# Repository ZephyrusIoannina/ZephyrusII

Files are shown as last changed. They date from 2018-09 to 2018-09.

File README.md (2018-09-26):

## Zephyrus II

This package was created by the Zephyrus II CanSat team (Ioannina - Greece) for the CanSats in Europe 2018 Launch campaign.
Feel free to use it as you please for future missions.
A reference to our team is most welcome but not obligatory.

The package contains:
1. Our source code for our flight module our payload and our groundstation with libraries. Extra effort was taken in translating our rem inside the code since it was mostly Greek
2. Our solidworks models
3. A calculations spreadsheet for data collected by our cansat
4. A spreadsheet with our calculation model for our descent
5. A list of commands for our cansat.
6. Electrical diagramms for both our modules

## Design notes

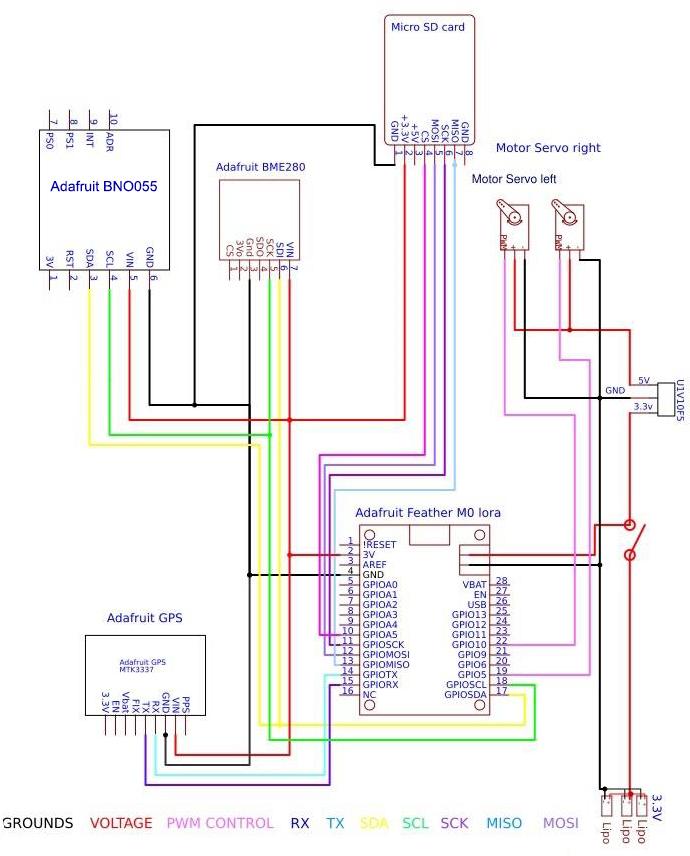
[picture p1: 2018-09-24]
flight electronics.jpg

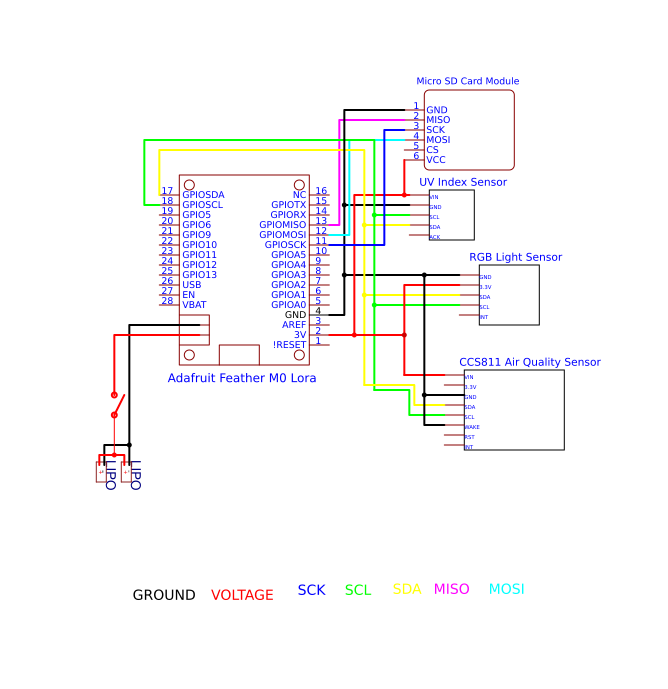
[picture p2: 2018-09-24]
payload.png

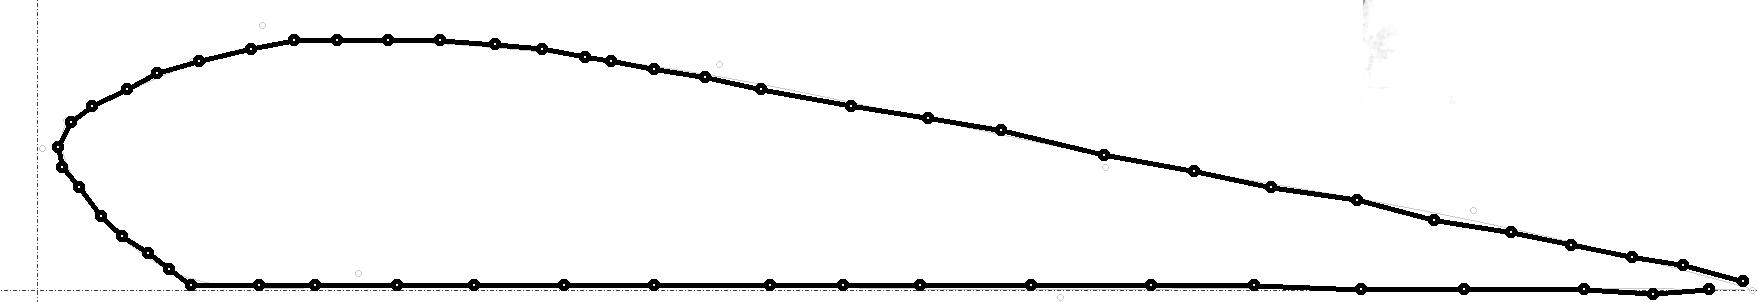
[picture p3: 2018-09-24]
zephyrusIIsolidworks/parachute/NS_foil.jpg

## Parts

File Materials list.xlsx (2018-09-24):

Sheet: Γενικά Υλικά για παραγγελίες
Αλεξίπτωτο |  |  |  |  | Ποσότητα | Τιμή μοναδας | Τελικό ποσό | Απαιτούνται
 | Ύφασμα | http://www.metropolis-drachen.de/en/Kite-materials/Cloth-Fabric/Spinnaker-fabrics/Spinnaker-Skytex-27.html |  |  | 8 | 11.90 € | 95.20 € | 1 | 11.90 €
 | Αυτοκόλητα επιδιόρθωσης | http://www.metropolis-drachen.de/en/Kite-materials/Stripes-Tapes/Tapes/Spi-repair-tape.html |  |  | 2 | 1.95 € | 3.90 € | 0 | 0.00 €
Flight Module
 | Radio - Arduino | https://gr.mouser.com/Search/ProductDetail.aspx?R=3179virtualkey54850000virtualkey485-3179 | 2km χαλαρα με απλη κεραια λεει | επι 4 μάλλον | 4 | 29.71 € | 118.84 € | 2 | 59.42 €
 | GPS | https://gr.mouser.com/Search/ProductDetail.aspx?R=746virtualkey54850000virtualkey485-746 | Serial |  | 2 | 33.96 € | 67.92 € | 1 | 33.96 €
 | Μαγνητόμετρο-Accel - Gyro | https://gr.mouser.com/ProductDetail/Adafruit/2472?qs=sGAEpiMZZMsMyYRRhGMFNuFoI0IaQxst8qeHhFTzrMI%3d | I2C |  | 2 | 30.00 € | 60.00 € | 1 | 30.00 €
 | Πίεση Θερμοκρασία Υγρασία | https://gr.mouser.com/Search/ProductDetail.aspx?R=2652virtualkey54850000virtualkey485-2652 | I2C |  | 2 | 16.96 € | 33.92 € | 1 | 16.96 €
ΙΔΙΟ μαγαζί | Esc | https://www.premium-modellbau.de/emax-bullet-20a-fpv-race-brushless-esc-2s-4s-3-5g-dshot-blheli-s |  |  | 2 | 15.90 € | 31.80 € | 1 | 15.90 €
 | Κινητήρας | https://www.premium-modellbau.de/emax-rs1106-fpv-racing-brushless-motor-7500kv-2s-7g | ΠΡΟΣΟΧΗ το 7500KV επιλέγουμε |  | 2 | 12.99 € | 25.98 € | 1 | 12.99 €
 | Έλικα (2x10) | https://www.premium-modellbau.de/t2345-emax-10x-paar-race-propeller-f.-rs1104-babyhawk-in-transparent |  | 20 κομμάτια | 1 | 19.95 € | 19.90 € | 0.05 | 1.00 €
 | Μπαταρία κινητήρα | http://www.giatrakos.gr/product/9793/perifereiaka-mpataries,-fortistes-mpataries-lipo-life-lrp-7.4v-900mah-vtec- |  |  | 2 | 15.00 € | 30.00 € | 1 | 15.00 €
 | SERVO PWM 120μοίρες | https://grobotronics.com/servo-micro-1.8kg.cm-metal-gears-feetech-fs90mg.html |  |  | 4 | 7.90 € | 31.60 € | 2 | 15.80 €
optional | Proximity Sensor | https://grobotronics.com/vcnl4000-proximity-light-sensor.html | I2C |  | 0 | 9.20 € | 0.00 € | 0 | 0.00 €
 | SD breakout | https://gr.mouser.com/Search/ProductDetail.aspx?R=254virtualkey54850000virtualkey485-254 |  |  | 4 | 6.38 € | 25.52 € | 2 | 12.76 €
 | μπαταρια διπλή flight | https://www.ebay.com/itm/3-7V-700mAh-Lipo-polymer-Li-Battery-cells-for-MP3-GPS-Camera-mobile-phone-702050/172452417339 |  |  | 4 | 6.40 € | 25.60 € | 2 | 12.80 € | http://www.giatrakos.gr/product/9623/perifereiaka-mpataries,-fortistes-mpataries-lipo-life-3.7v-750mah-syma-battery-
Payload Module ϊσως βολεύει 3,3 Volt όλο το module
 | Radio - Arduino | https://www.adafruit.com/product/3179
 | μπαταρία payload | https://www.ebay.com/itm/2pcs-3-7V-700mAh-lipo-Polymer-li-cells-Battery-For-Mp3-GPS-camera-DVD-PAD-803030/262501223843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 | διπλή |  | 4 | 8.93 € | 35.72 € | 2 | 17.86 €
 | UV sensor | https://gr.mouser.com/Search/ProductDetail.aspx?R=2899virtualkey54850000virtualkey485-2899 | I2C |  | 2 | 5.06 € | 10.12 € | 1 | 5.06 €
 | Light sensor | https://gr.mouser.com/Search/ProductDetail.aspx?R=SEN-12829virtualkey54740000virtualkey474-SEN-12829 | I2C | RGB!! | 2 | 6.76 € | 13.52 € | 1 | 6.76 €
out of stock (μόνο1) | CO2 VOC | https://www.hellasdigital.gr/electronics/sensors/gas-sensors/adafruit-ccs811-air-quality-sensor-breakout-voc-and-eco2/ |  |  | 2 | 24.80 € | 49.60 € | 1 | 24.80 € |  | out of stock
 |  |  |  | Σύνολο |  |  | 679.14 € |  | 292.97 €
 |  |  |  |  |  |  |  |  | Κόστος Cansat
 | Σταθεροποιητής | Voltage Regulator L7805CV - 5V 1.5AΚωδικός: 05-00078050 (https://grobotronics.com/voltage-regulator-l7805cv-5v-1.5a.html)
 | Σταθεροποιητής | Voltage Regulator LD1117 - 3.3V 800mAΚωδικός: 05-01117330 (https://grobotronics.com/voltage-regulator-ld1117-3.3v-800ma.html)

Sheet: Κοστολόγιο Υλικών Cansat
Αλεξίπτωτο |  |  |  |  | Ποσότητα | Τιμή μοναδας | Τελικό ποσό
 | Ύφασμα | http://www.metropolis-drachen.de/en/Kite-materials/Cloth-Fabric/Spinnaker-fabrics/Spinnaker-Skytex-27.html |  |  | 1 | 11.90 € | 11.90 €
 | Αυτοκόλητα επιδιόρθωσης | http://www.metropolis-drachen.de/en/Kite-materials/Stripes-Tapes/Tapes/Spi-repair-tape.html |  |  | 1 | 1.95 € | 1.95 €
 | Σχοινιά
Flight Module
 | Radio - Arduino | https://gr.mouser.com/Search/ProductDetail.aspx?R=3179virtualkey54850000virtualkey485-3179 | 2km χαλαρα με απλη κεραια λεει | επι 4 μάλλον | 1 | 29.71 € | 29.71 €
 | GPS | https://gr.mouser.com/Search/ProductDetail.aspx?R=746virtualkey54850000virtualkey485-746 | Serial |  | 1 | 33.96 € | 33.96 €
 | Μαγνητόμετρο-Accel - Gyro | https://gr.mouser.com/ProductDetail/Adafruit/2472?qs=sGAEpiMZZMsMyYRRhGMFNuFoI0IaQxst8qeHhFTzrMI%3d | I2C |  | 1 | 30.00 € | 30.00 €
 | Πίεση Θερμοκρασία Υγρασία | https://gr.mouser.com/Search/ProductDetail.aspx?R=2652virtualkey54850000virtualkey485-2652 | I2C |  | 1 | 16.96 € | 16.96 €
ΙΔΙΟ μαγαζί | Esc | https://www.premium-modellbau.de/emax-bullet-20a-fpv-race-brushless-esc-2s-4s-3-5g-dshot-blheli-s |  |  | 0 |  | 0.00 €
 | Κινητήρας | https://www.premium-modellbau.de/emax-rs1106-fpv-racing-brushless-motor-7500kv-2s-7g | ΠΡΟΣΟΧΗ το 7500KV επιλέγουμε |  |  |  | 0.00 €
 | Έλικα (2x10) | https://www.premium-modellbau.de/t2345-emax-10x-paar-race-propeller-f.-rs1104-babyhawk-in-transparent |  |  |  |  | 1.00 €
 | Μπαταρία | http://www.giatrakos.gr/product/9793/perifereiaka-mpataries,-fortistes-mpataries-lipo-life-lrp-7.4v-900mah-vtec- |  |  | 1 | 15.00 € | 15.00 € | απο giatrakos
 | SERVO PWM 120μοίρες | https://grobotronics.com/servo-micro-1.8kg.cm-metal-gears-feetech-fs90mg.html |  |  | 2 | 7.90 € | 15.80 € | απο grobotr
 | SD breakout | https://gr.mouser.com/Search/ProductDetail.aspx?R=254virtualkey54850000virtualkey485-254 |  |  | 1 | 6.38 € | 6.38 €
 | μπαταρια 2 | http://www.giatrakos.gr/product/9623/perifereiaka-mpataries,-fortistes-mpataries-lipo-life-3.7v-750mah-syma-battery- |  |  | 2 | 10.00 € | 20.00 € | απο giatrakos
Payload Module ϊσως βολεύει 3,3 Volt όλο το module
 | Radio - Arduino | https://gr.mouser.com/Search/ProductDetail.aspx?R=3179virtualkey54850000virtualkey485-3179 |  |  | 1 | 29.71 € | 29.71 € | https://www.adafruit.com/product/3179
 | UV sensor | https://gr.mouser.com/Search/ProductDetail.aspx?R=2899virtualkey54850000virtualkey485-2899 | I2C |  | 1 | 5.06 € | 5.06 €
 | Light sensor | https://gr.mouser.com/Search/ProductDetail.aspx?R=SEN-12829virtualkey54740000virtualkey474-SEN-12829 | I2C | RGB!! | 1 | 6.76 € | 6.76 €
 | CO2 VOC | https://www.hellasdigital.gr/electronics/sensors/gas-sensors/adafruit-ccs811-air-quality-sensor-breakout-voc-and-eco2/ |  |  | 1 | 24.80 € | 24.80 € | https://gr.mouser.com/Search/ProductDetail.aspx?R=3566virtualkey54850000virtualkey485-3566 | out of stock
 |  |  |  | Σύνολο |  |  | 248.99 €

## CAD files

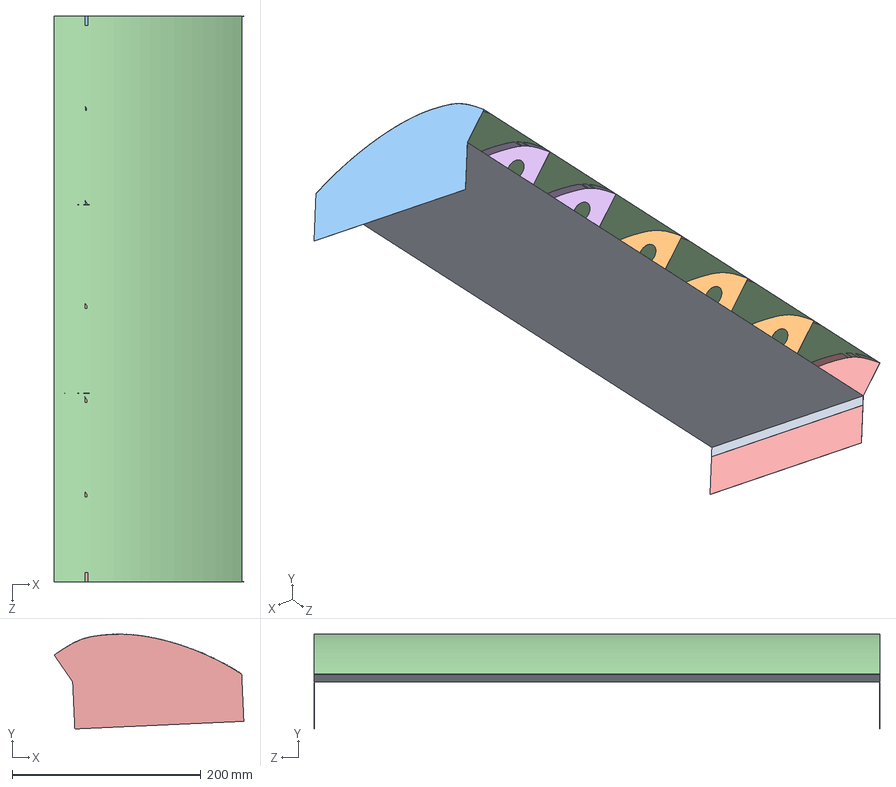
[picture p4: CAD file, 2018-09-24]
zephyrusIIsolidworks/parachute/Assem1a.SLDASM
201.2 x 100.7 x 600.2 mm
bottom
compartement x 3
sideb
top
side
compartement_L x 2

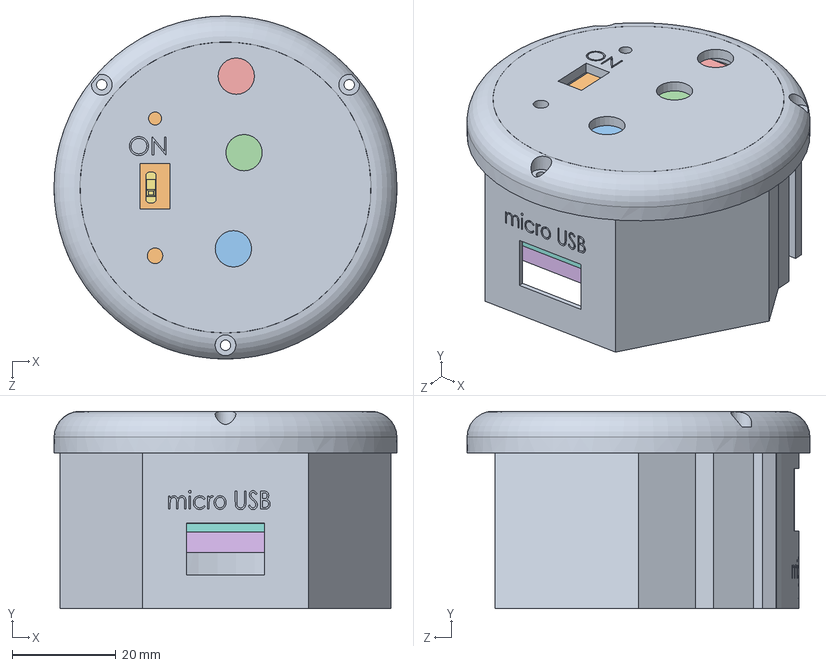
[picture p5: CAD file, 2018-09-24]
zephyrusIIsolidworks/PAYLOAD_ASSEMB.SLDASM
66.0 x 38.0 x 66.0 mm
payload
perfboard_pl
CCS811
ISL29125
VEML6070
featherM0LORA
SMD Switch
perfboard_pl_2
perfboard_pl_3
Micro SD
Lipo750A

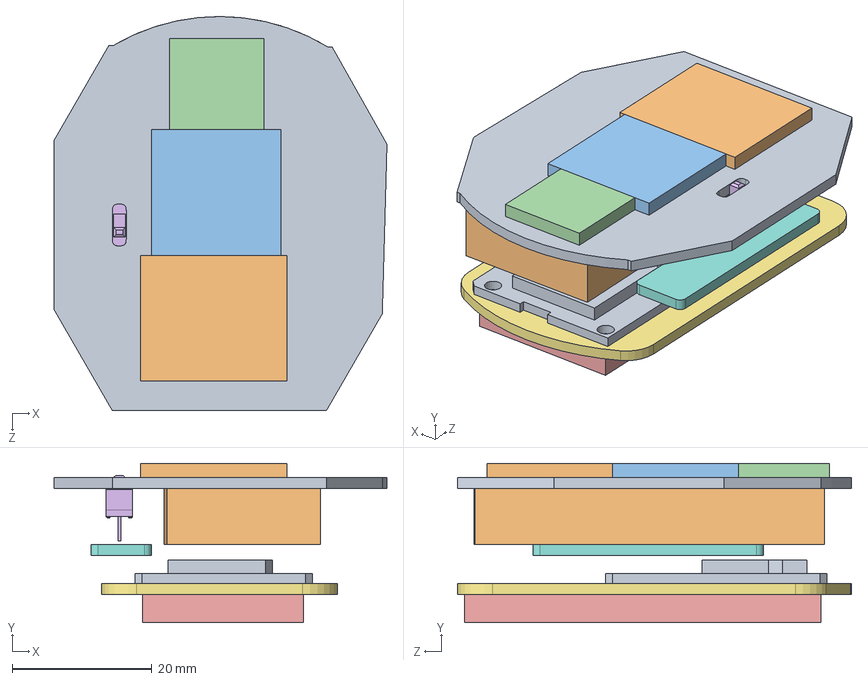
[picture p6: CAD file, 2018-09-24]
zephyrusIIsolidworks/perf_payload.SLDASM
47.7 x 22.8 x 56.4 mm
perfboard_pl
CCS811
ISL29125
VEML6070
featherM0LORA
SMD Switch
perfboard_pl_2
perfboard_pl_3
Micro SD
Lipo750A

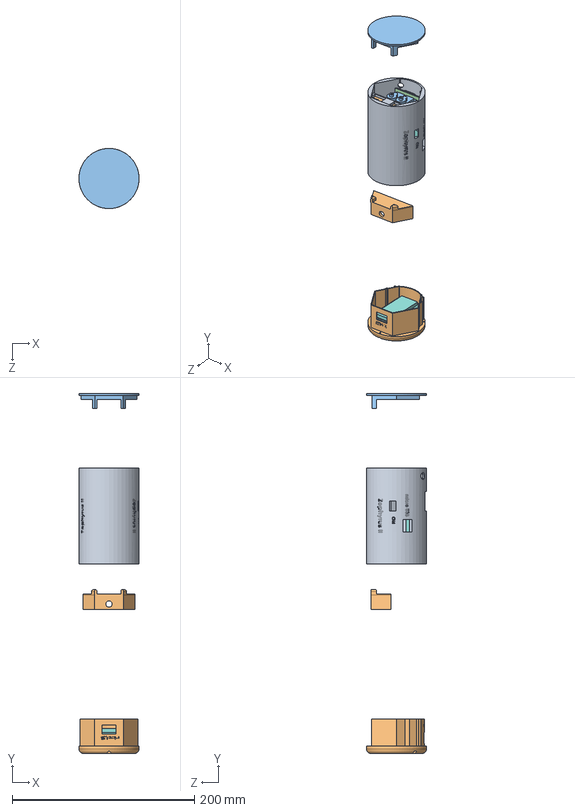
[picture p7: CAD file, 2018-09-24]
zephyrusIIsolidworks/Assem1nobat2.SLDASM
66.0 x 395.0 x 66.0 mm
Flight_down_nobat_2
Lipo750A x 4
Tower Pro 9g Micro Servo SG90 x 2
perfboard
Adafruit BME280
GPS
BNO055
featherM0LORA x 2
Micro SD x 2
payload
perfboard_pl
CCS811
ISL29125
VEML6070
SMD Switch
perfboard_pl_2
perfboard_pl_3
batterycap
backcap

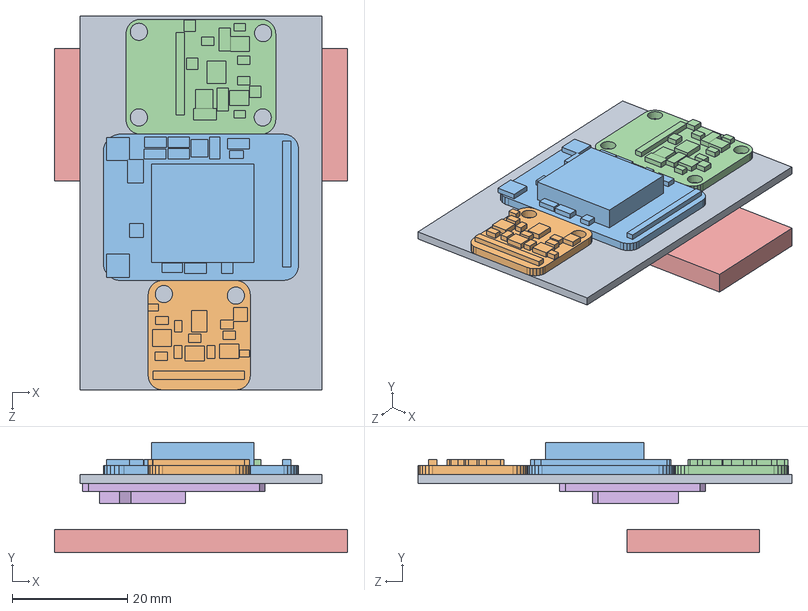
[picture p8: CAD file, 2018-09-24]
zephyrusIIsolidworks/perf_flight.SLDASM
51.0 x 19.2 x 65.0 mm
perfboard
Adafruit BME280
GPS
BNO055
featherM0LORA
Micro SD

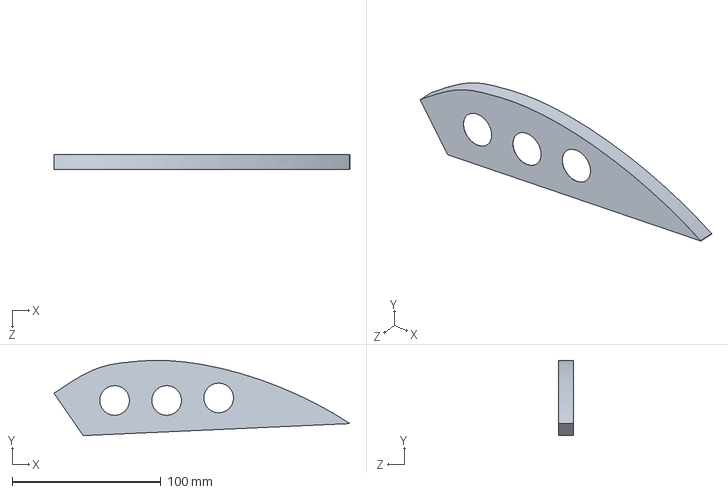
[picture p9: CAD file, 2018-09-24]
zephyrusIIsolidworks/parachute/compartement_L.SLDPRT
199.0 x 50.6 x 10.1 mm

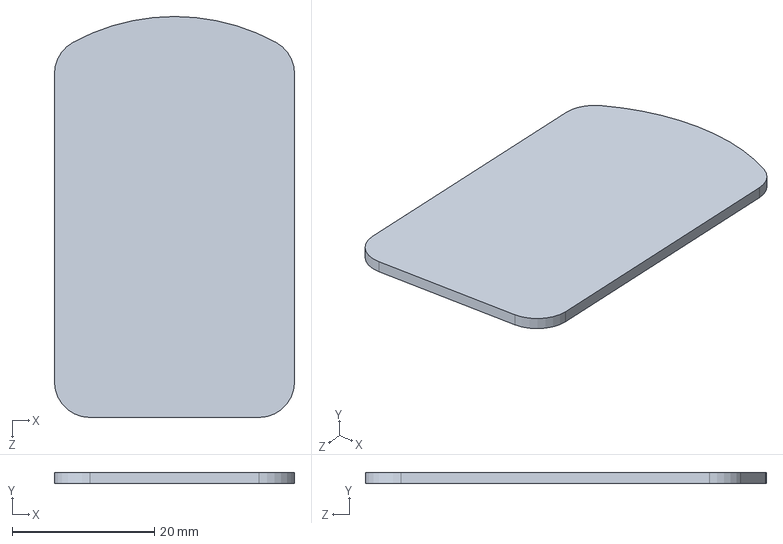
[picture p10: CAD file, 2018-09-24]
zephyrusIIsolidworks/perfboard_pl_2.SLDPRT
33.8 x 1.60 x 56.4 mm

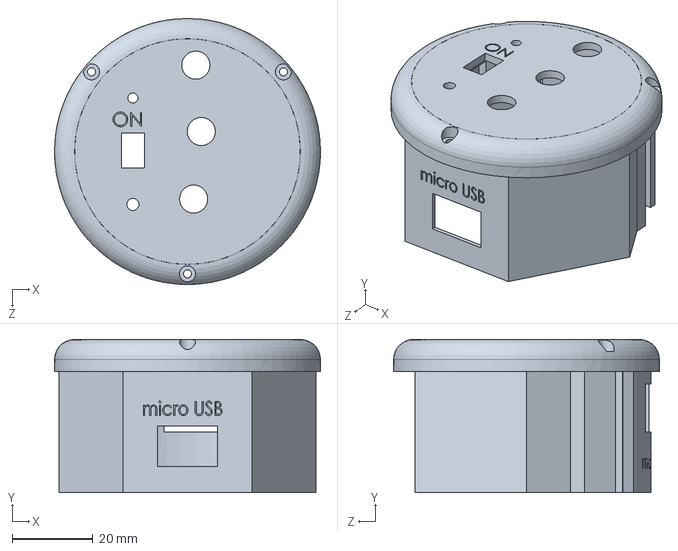
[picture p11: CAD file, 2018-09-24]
zephyrusIIsolidworks/payload.SLDPRT
66.0 x 38.0 x 66.0 mm

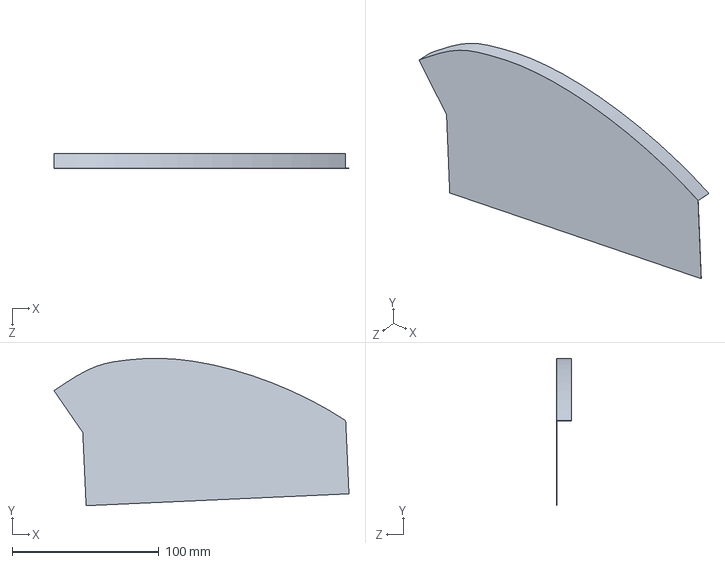
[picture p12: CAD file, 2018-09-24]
zephyrusIIsolidworks/parachute/side.SLDPRT
201.2 x 100.5 x 10.0 mm

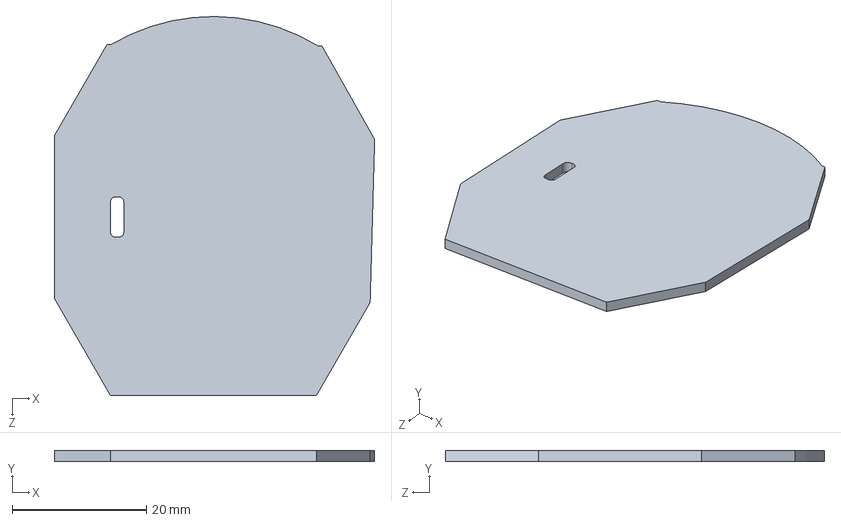
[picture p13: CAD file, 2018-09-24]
zephyrusIIsolidworks/perfboard_pl.SLDPRT
47.7 x 1.60 x 56.4 mm

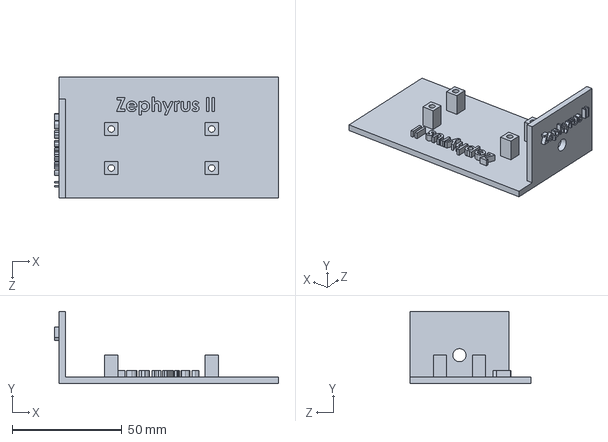
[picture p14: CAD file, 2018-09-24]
zephyrusIIsolidworks/groundstation.SLDPRT
102.0 x 33.0 x 55.0 mm

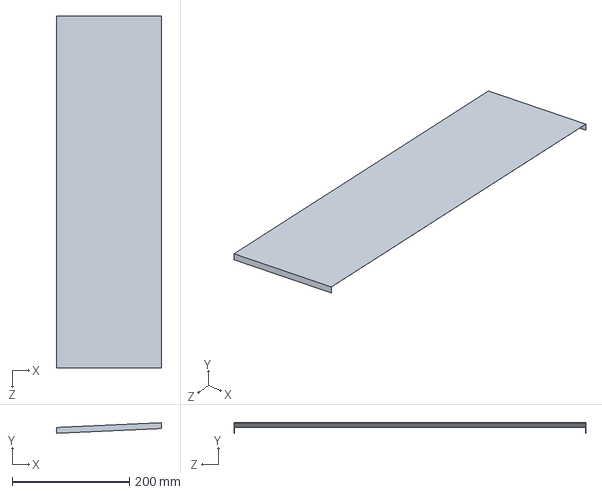
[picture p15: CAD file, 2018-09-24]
zephyrusIIsolidworks/parachute/bottom.SLDPRT
179.8 x 18.1 x 600.0 mm

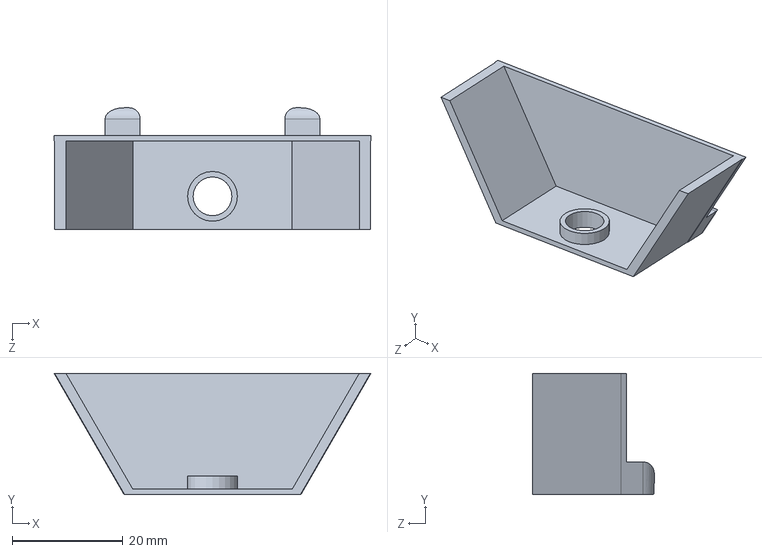
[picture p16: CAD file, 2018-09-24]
zephyrusIIsolidworks/batterycap.SLDPRT
57.2 x 21.9 x 22.0 mm

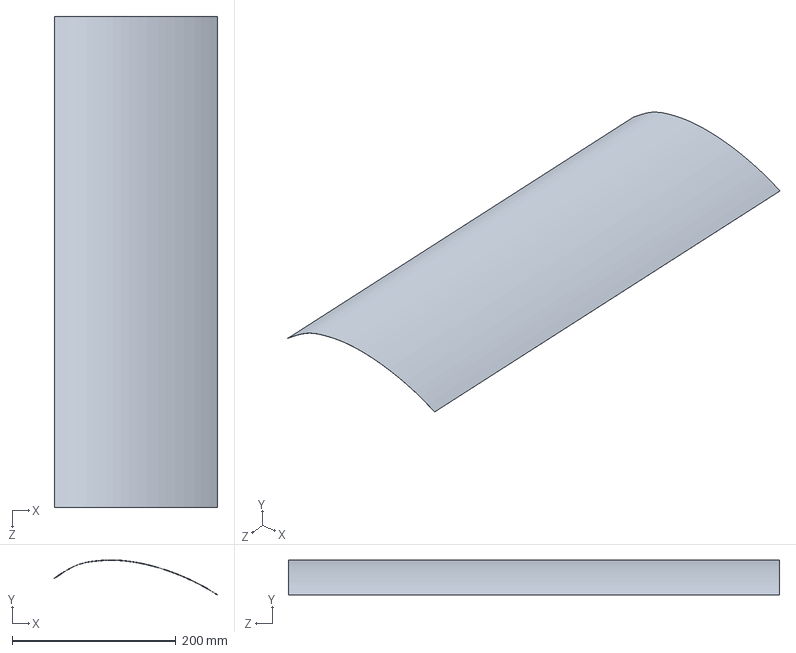
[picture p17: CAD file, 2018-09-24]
zephyrusIIsolidworks/parachute/top.SLDPRT
199.1 x 42.6 x 600.2 mm

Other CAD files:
zephyrusIIsolidworks/parachute/compartement.SLDPRT
zephyrusIIsolidworks/parachute/sideb.SLDPRT
zephyrusIIsolidworks/perfboard_pl_3.SLDPRT
zephyrusIIsolidworks/parachute/compartement_L_2.SLDPRT
zephyrusIIsolidworks/Flight_down_nobat_2.SLDPRT
zephyrusIIsolidworks/backcap.SLDPRT
zephyrusIIsolidworks/parachute/compartement_sketch.SLDDRW
zephyrusIIsolidworks/parachute/compartement_sketch.SLDPRT
zephyrusIIsolidworks/parachute/compartement_sketch_large.STL
zephyrusIIsolidworks/perfboard.SLDPRT

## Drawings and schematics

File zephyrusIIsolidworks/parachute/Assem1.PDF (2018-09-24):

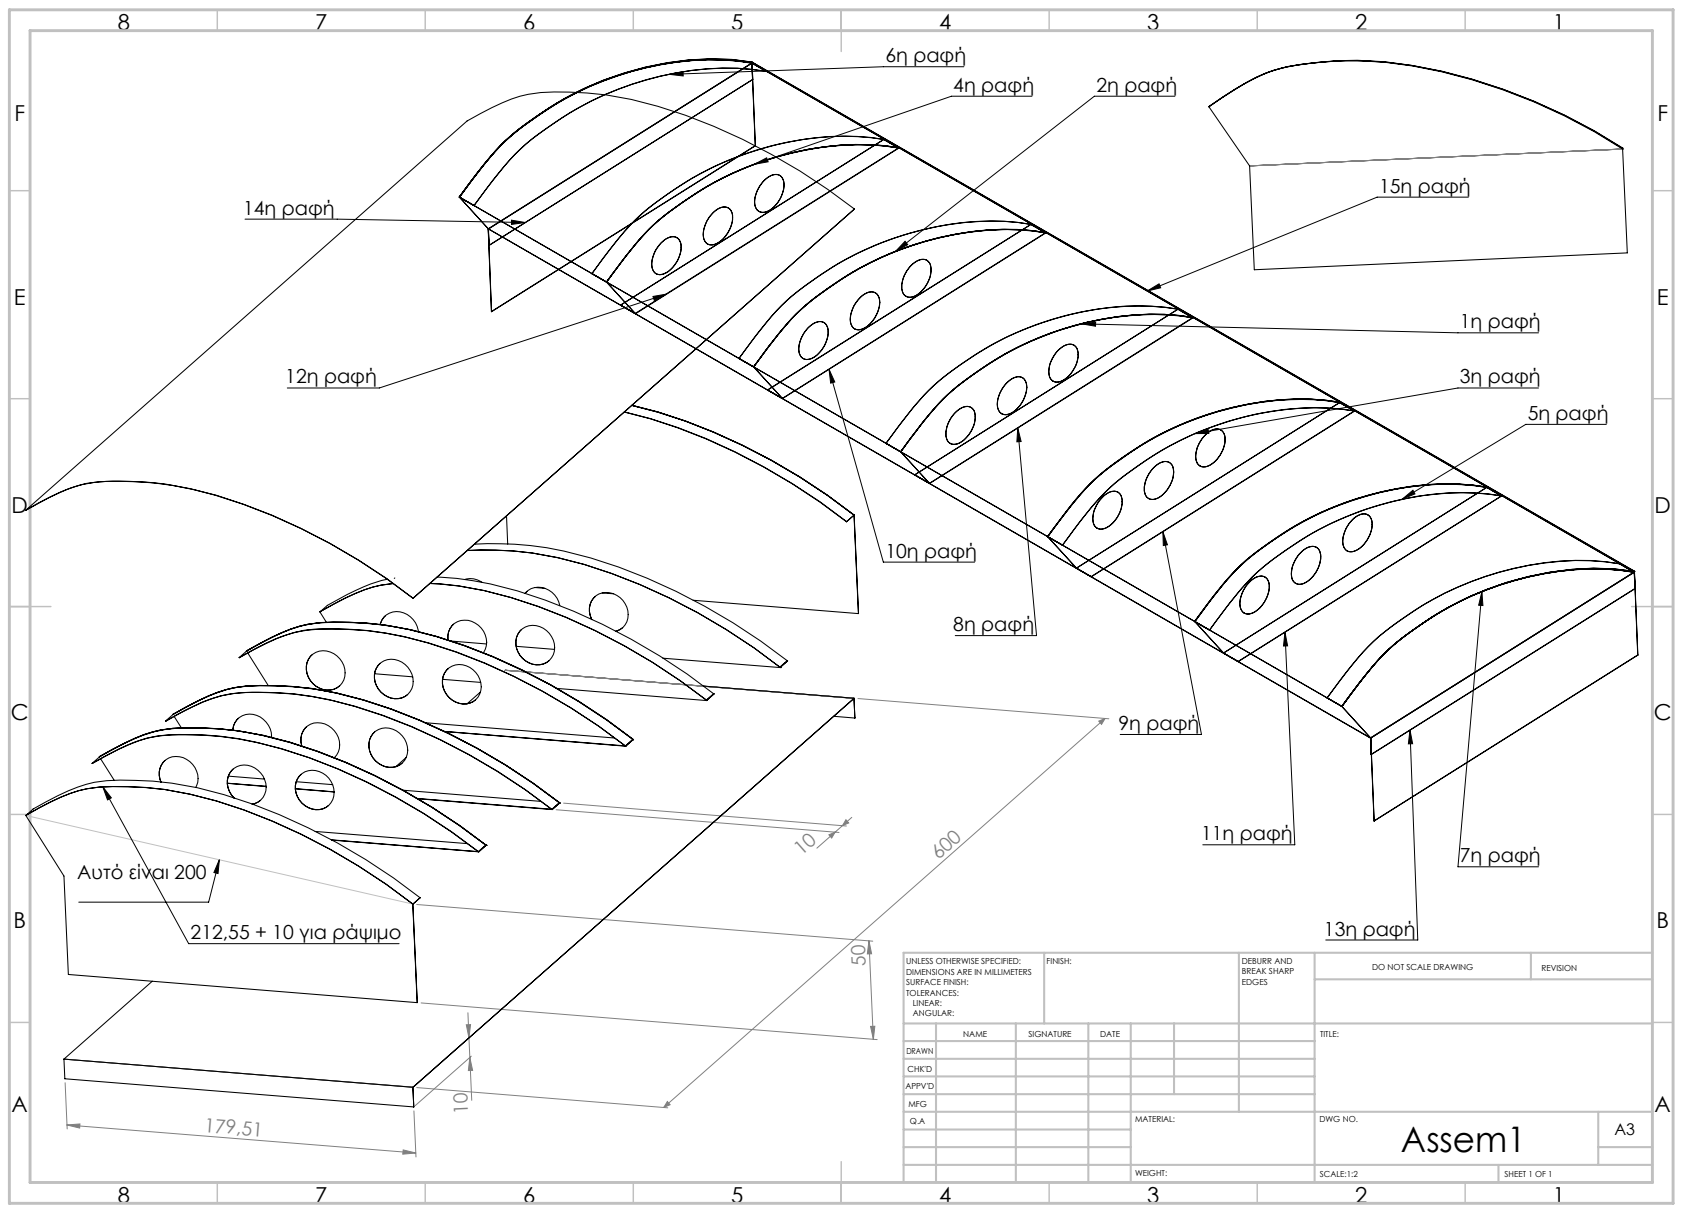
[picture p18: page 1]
1η ραφή; 2η ραφή; 3η ραφή; 4η ραφή; 5η ραφή; 6η ραφή; 7η ραφή; 8η ραφή; 9η ραφή; 10η ραφή; 11η ραφή; 12η ραφή; 13η ραφή; 14η ραφή; 15η ραφή; 212,55 + 10 για ράψιμο; Αυτό είναι 200; FINISH:; DEBURR AND; BREAK SHARP; DO NOT SCALE DRAWING; REVISION; SCALE:1:2; SHEET 1 OF 1

UNLESS OTHERWISE SPECIFIED:
DIMENSIONS ARE IN MILLIMETERS
SURFACE FINISH:
TOLERANCES:
LINEAR:
ANGULAR:

NAME | SIGNATURE | DATE | | | | TITLE:

DRAWN
CHK'D
APPV'D
MFG
Q.A | | | | MATERIAL: | DWG NO. Assem1 | A3

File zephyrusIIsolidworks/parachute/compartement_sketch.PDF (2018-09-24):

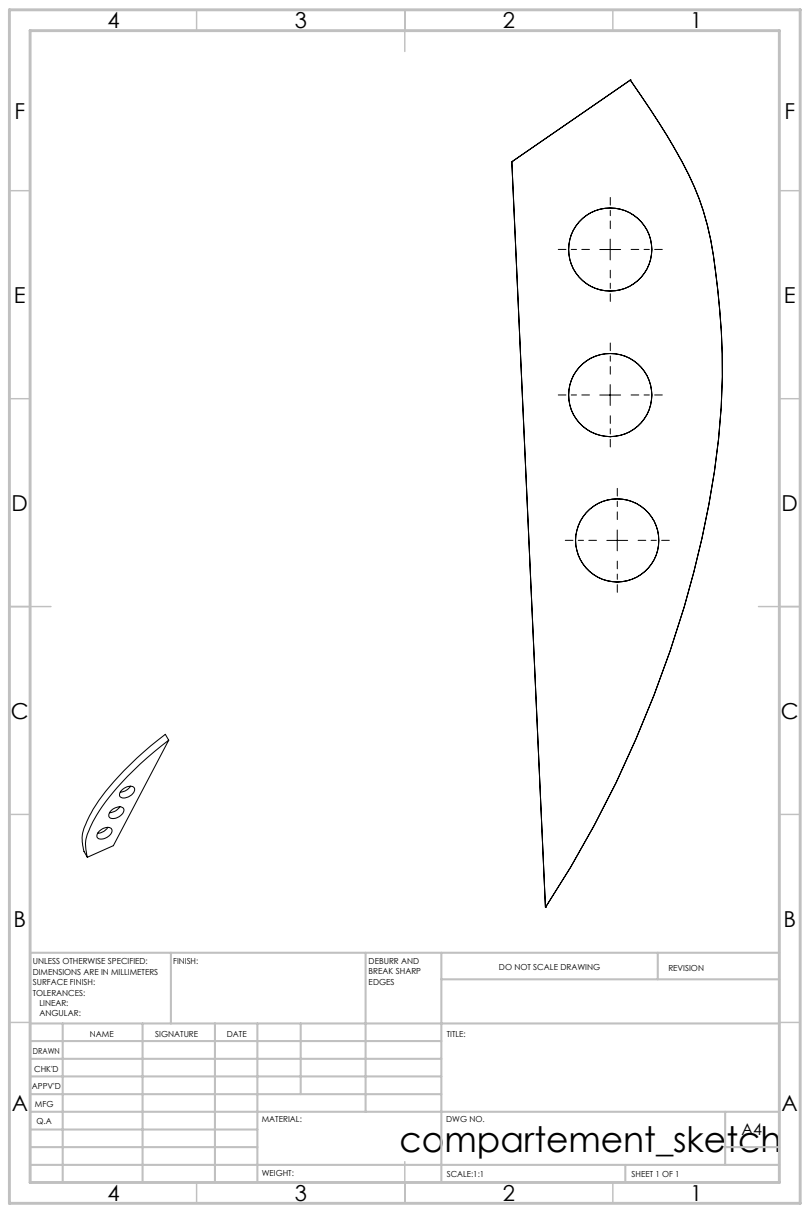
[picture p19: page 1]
FINISH:; DEBURR AND; BREAK SHARP; DO NOT SCALE DRAWING; REVISION; SCALE:1:1; SHEET 1 OF 1

UNLESS OTHERWISE SPECIFIED:
DIMENSIONS ARE IN MILLIMETERS
SURFACE FINISH:
TOLERANCES:
LINEAR:
ANGULAR:

NAME | SIGNATURE | DATE | | | | TITLE:

DRAWN
CHK'D
APPV'D
MFG
Q.A | | | | MATERIAL: compartement_sketch | DWG NO. | A4

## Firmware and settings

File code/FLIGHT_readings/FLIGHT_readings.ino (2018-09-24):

//Include the required libraries

#include <Wire.h>
#include <SPI.h>
#include <Timer.h>
#include <SD.h>
#include <Adafruit_Sensor.h>
#include <Adafruit_BME280.h> //Pressure,Temp,Humidity
#include <Adafruit_GPS.h> // Gps
#include <RH_RF95.h> // Radio lora 433Mhz
#include <Adafruit_BNO055.h>// Absolute orientation sensor
#include <utility/imumaths.h>// Absolute orientation maths
#include <PID_v1.h> // Pid Code
#include <Servo.h> // Servo library

// Blinky on receipt
#define LED 13

//sd card set chipselect
const int chipSelect = 11;

char serialdata[14]; //  This is the buffer from the serial port
char initcom[4]; // Check the first 3 letters of each command recieved - Look for command
char noletters[10];// The other 9 letters are command values

//define timers ---------------------------------
Timer t;
Timer t2;
Timer ta;
Timer tb;
Timer tc;
//PID parameters------------------------------------
// Define Variables we'll be connecting to
double Setpoint, Input, Output;

// Define the aggressive and conservative Tuning Parameters
double aggKp = 4, aggKi = 0.2, aggKd = 1;
double consKp = 1, consKi = 0.05, consKd = 0.25;

//Specify the links and initial tuning parameters
PID myPID(&Input, &Output, &Setpoint, consKp, consKi, consKd, DIRECT);

float PIDstatus;  // This value is to be set with a command to choose the servo mode
//float testDiff; // Testing

//Battery levels Parameters -------------------------------------
#define VBATPIN A7

//servo parameters
Servo myservoL;  // Create  servo object to control servo Left
Servo myservoR;  // Create  servo object to control servo Right

int posR = 115;    // Variable to store the servo position Right
int posL = 5;    // Variable to store the servo position Left
int maxAngle; // Max allowed servo angle  -  Max allowed is 110 degrees
float maxAng; // Same as the above but in float 

//BNO055 Parameters-------------------------------------------------
Adafruit_BNO055 bno = Adafruit_BNO055(55);

//BME280 parameters ----------------------------------------------------
#define SEALEVELPRESSURE_HPA (1013.25)
Adafruit_BME280 bme; // I2C
int P, T, H, Ap, Apold; // Integers to be send -  pressure,temp,humidity,Altitude(by pressure), previous altitude

//Radio Parameters -------------------------
/* for feather m0  */

#define RFM95_CS 8
#define RFM95_RST 4
#define RFM95_INT 3

// Change to 434.0 or other frequency, must match RX's freq!
#define RF95_FREQ 433.55


// Singleton instance of the radio driver
RH_RF95 rf95(RFM95_CS, RFM95_INT);


char apostoli[100];
char apostoliB[100];
char fdata[100]; // Selected flight parameters data
char reply[10];

//GPS Parameters -------------------------
// Set GPSECHO to 'false' to turn off echoing the GPS data to the Serial console
// Set to 'true' if you want to debug and listen to the raw GPS sentences
#define GPSECHO false
// this keeps track of whether we're using the interrupt
// off by default!
boolean usingInterrupt = false;
//GPS hardware serial - Cannot use software serial
Adafruit_GPS GPS(&Serial1);



//--------------------------------------------------|
//                    WAYPOINTS                     |
//--------------------------------------------------|
//Please enter the latitude and longitude of your   |
// A site to acquire cordinates
//https://www.gps-coordinates.net/
//desired destination:  (Test - School)         39.660363,20.851830,  |
//39.698092, 20.772974
//north - 39.719097, 20.820682
//north + 39.722688, 20.835791
#define GEO_LAT                38.046410
#define GEO_LON                23.401782
//default ligkiades
//--------------------------------------------------|
// Navigation location
float targetLat = GEO_LAT; // Latitude of target
float targetLon = GEO_LON; // longitude of target
float targetAlt = 100; //  Threshold altitude after which we are  in landing mode 
float startingAlt = 500; // Altitude when Pid starts
// Trip distance
float tripDistance;  // Distance from target
long dist;            // Distance from target in long for beaming to the groundstation
float fHeading;    // direction to the set target in relation to the north
int heading;      //  direction to the set target in relation to the northh in Int for beaming to the groundstation
float maxaccX;
float maxaccY;
float maxaccZ;
//float maxACCEL; // Max acceleration in each calculation cycle
//double headingpid;
boolean isStarted = false;
long interval;
long previousMillis;


//Reply Messages -------------------------
char message1[] = {"Flight_Reply1"};
char message2[] = {"Flight_Reply2"};
char message3[] = {"target_UOI"};
char message4[] = {"Dump_SDserial"};
char message5[] = {"Erase_SD_data"};

int val;

void setup()
{
  //Initialize serial connection for debugging
  Serial.begin(9600);

  // GPS SETUP----------------------------------------
  GPS.begin(9600);
  GPS.sendCommand(PMTK_SET_NMEA_OUTPUT_RMCGGA);
  // GPS.sendCommand(PMTK_SET_NMEA_UPDATE_200_MILLIHERTZ);
  GPS.sendCommand(PMTK_SET_NMEA_UPDATE_1HZ); // Set the update rate
  GPS.LOCUS_StartLogger(); //start GPS internal memory logger
  /*  GPS.sendCommand("$PMTK185,1*23");  // Stops the logger.
  */


  //Servo attach to pins
  myservoR.attach(5);  // attaches the servo on pin 5 to the servo object
  myservoL.attach(10);  // attaches the servo on pin 10 to the servo object

  myservoR.write(posR);
  myservoL.write(posL);

  PIDstatus = 23;
  maxAngle = 60;
  //  testDiff = -180;
  //PIDstatus

  delay(2000);

  // BME280 SETUP ---------------------------------------
  bool status;
  status = bme.begin();
  if (!status) {
    Serial.println("Could not find a valid BME280 sensor, check wiring!");
    //while (1);
  }
  // BNO055 SETUP --------------------------------
  if (!bno.begin())
  {
    /* There was a problem detecting the BNO055 ... check your connections */
    Serial.print("Ooops, no BNO055 detected ... Check your wiring or I2C ADDR!");
    //while(1);
  }
  delay(1000);
  bno.setExtCrystalUse(true);

  maxaccX = 0;
  maxaccY = 0;
  maxaccZ = 0;

  //Radio SETUP --------------------------------

  pinMode(RFM95_RST, OUTPUT);
  digitalWrite(RFM95_RST, HIGH);
  delay(100);

  Serial.println("Feather LoRa TX Test!");

  // manual reset
  digitalWrite(RFM95_RST, LOW);
  delay(10);
  digitalWrite(RFM95_RST, HIGH);
  delay(10);

  while (!rf95.init()) {
    Serial.println("LoRa radio init failed");
    //while (1);
  }
  Serial.println("LoRa transmit radio init OK!");
  // Defaults after init are 434.0MHz, modulation GFSK_Rb250Fd250, +13dbM
  if (!rf95.setFrequency(RF95_FREQ)) {
    Serial.println("setFrequency failed");
    //while (1);
  }
  Serial.print("Set Freq to: "); Serial.println(RF95_FREQ);

  // Defaults after init are 434.0MHz, 13dBm, Bw = 125 kHz, Cr = 4/5, Sf = 128chips/symbol, CRC on
  // The default transmitter power is 13dBm, using PA_BOOST.
  // If you are using RFM95/96/97/98 modules which uses the PA_BOOST transmitter pin, then
  // you can set transmitter powers from 5 to 23 dBm:
  rf95.setTxPower(23, false);

  delay(500); //for everything to initialize

  //SD Card SETUP ---------------

  // put after Radio initiallization
  //8 is the actual CS pin for the feather.
  //It is inaccesible and used by the radio but must be HIGH in order for sd to work no matter what CS pin for sd is used.
  // pinMode(8, OUTPUT);//unrem if radio off
  //digitalWrite(8, HIGH);//unrem if radio off
  Serial.print("Initializing SD card...");
  if (!SD.begin(chipSelect)) {
    Serial.println("initialization failed!");
    //return;
  }
  Serial.println("initialization done.");

  //PID setup----------------------------------
  // The input is the value for headingpid
  Setpoint = 0; // Is made the value of the actual heading
  //turn the PID on
  myPID.SetMode(AUTOMATIC);

  //Timers SETUP ---------------
  t.every (1000, steiledata); // After how much time is the function senddata  
  t2.every(5000, steiledataB); //After how much time is the function senddata
  tb.every(200, BNOvalues); //After how much time is the function BNOvalues
  tc.every(1000, pidfunction);//After how much time is the function Pidfunction
}
//^^^^^^^^^^^^^^^^^^^^^^^^^^^^^^ VOID LOOP ^^^^^^^^^^^^^^^^^^^^^^^^^^^^^^^^^^^^^^
void loop()
{

  //Receive NMEA phrase from GPS -  Cannot be made into function---It doesnt work---
  char c = GPS.read();
  if (GPS.newNMEAreceived()) {
    // a tricky thing here is if we print the NMEA sentence, or data
    // we end up not listening and catching other sentences!
    // so be very wary if using OUTPUT_ALLDATA and trytng to print out data
    //Serial.println(GPS.lastNMEA());   // this also sets the newNMEAreceived() flag to false
  }
  if (!GPS.parse(GPS.lastNMEA())) {  // this also sets the newNMEAreceived() flag to false
    //return;  // we can fail to parse a sentence in which case we should just wait for another
    Serial.print("");
  }

  //update timers ------------------------
  t.update();//update timer
  t2.update(); //update timer
  tb.update();//update timer
  tc.update();//update timer


  // -------an pirame kapoia entoli tote... ------------

  uint8_t buf[RH_RF95_MAX_MESSAGE_LEN];
  uint8_t len = sizeof(buf);

  if (rf95.recv(buf, &len))
  {
    Serial.print("RSSI,");
    Serial.print(rf95.lastRssi(), DEC); Serial.print(",");
    Serial.println((char*)buf);

    // Everything received from the radio module is also saved on the sd card. In this  way we backup each modules data to both modules 
    /* File dataFile = SD.open("datalog.txt", FILE_WRITE);
    if (dataFile) {
      dataFile.println((char*)buf);
      dataFile.close();
    }*/

    //Split the buffer in pieces to check for commands
    memcpy(initcom, &buf[0], 3 ); // First three letters of what we received
    memcpy(noletters, &buf[3], 10 );// The following 9
    initcom[4] = '\0';  //End of array
    noletters[10] = '\0';  //End of array

    // Serial.println(initcom);
    // Serial.println(noletters);

  }
  if (strlen((char*)buf) > 0)
  {
    if (strcmp_P((char*)buf, "gpsA") == 0)    // Compares Ram to Flash memory
    {
      gpsA();
    }
    else if (strcmp_P((char*)buf, "gpsB") == 0)
    {
      gpsB();
    }
    else if (strcmp_P((char*)buf, "gpsC") == 0)
    {
      gpsC();
    }
    else if (strcmp_P((char*)buf, "gpsD") == 0)
    {
      gpsD();
    }
    else if (strcmp_P((char*)buf, "FdumpSD") == 0)
    {
      FdumpSD();
    }
    else if (strcmp_P((char*)buf, "FdeleteSD") == 0)
    {
      FdeleteSD();
    }
    else if (strcmp_P((char*)buf, "flight") == 0)
    {
      flightdata();
    }
    else if (strcmp_P((char*)initcom, "ang") == 0)
    {
      chAngle();
    }
    else if (strcmp_P((char*)initcom, "lat") == 0)
    {
      changelat();
    }
    else if (strcmp_P((char*)initcom, "lon") == 0)
    {
      changelon();
    }
    else if (strcmp_P((char*)initcom, "alt") == 0)
    {
      changealt();
    }
    else if (strcmp_P((char*)initcom, "pid") == 0)
    {
      changepid();
    }
    /*else if (strcmp_P((char*)initcom, "dif") == 0)
      {
      testDiff = atof(noletters);
      }*/

  }
  void clearRxBuf(); //καθαρισμός buffer λήψης
  memset(buf, 0, sizeof(buf)); //Deletes the variable buf


  //-----------------receive command from serial ----------------------

  while (Serial.available()) {    //As long as something is received in serial port
    Serial.readBytes(serialdata, 14); //We use readbytes as it used below for beaming to the groundstation,  Serial.readString is not converted
    Serial.println(serialdata);

    if (strcmp_P((char*)serialdata, "FdumpSD") == 0)
    {
      FdumpSD();
    }
    if (strcmp_P((char*)serialdata, "FdeleteSD") == 0)
    {
      FdeleteSD();
    }
    if (strcmp_P((char*)serialdata, "gpsC") == 0) {
      gpsC();
    }
    if (strcmp_P((char*)serialdata, "gpsA") == 0) {
      gpsA();
    }
    if (strcmp_P((char*)serialdata, "gpsB") == 0) {
      gpsB();
    }
    if (strcmp_P((char*)serialdata, "deleteGPS") == 0) {
      deleteGPS();
    }
    if (strcmp_P((char*)serialdata, "dumpGPS") == 0) {
      dumpGPS();
    }
    else {
    }
  }
  memset(serialdata, 0, sizeof(serialdata)); //Deletes the serialdata variable
  // if you want to debug, this is a good time to do it!
  if (GPSECHO)
    if (c) Serial.print(c);
}

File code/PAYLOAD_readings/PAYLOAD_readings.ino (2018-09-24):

//Include the required libraries

#include <Wire.h>
#include <SPI.h>
#include <Timer.h> 
#include <SD.h> 
#include <Adafruit_Sensor.h>
#include "SparkFunISL29125.h" //uv sensor
#include "Adafruit_CCS811.h" //vocs sensor
#include <RH_RF95.h> //radio lora 433Mhz
#include "Adafruit_VEML6070.h" //UV intensity sensor


// Blinky on receipt
#define LED 13

//sd card set chipselect
const int chipSelect = 10;

//---Variables for synchronisation
char trig[2];// First letter buffer
unsigned long beforeMillis;
unsigned long afterMillis;
unsigned long duration;

//Battery levels Parameters -----------------------
#define VBATPIN A7

// Commands for comparison to flash memory
/*const char s1[] PROGMEM = {"epayload1"};
const char s2[] PROGMEM = {"epayload2"};
const char s3[] PROGMEM = {"epayload3"};
const char s4[] PROGMEM = {"epayload4"};
const char s5[] PROGMEM = {"epayload5"};
*/
//define timers -------------------
Timer t;

//UV sensor Parameters -------------------------
Adafruit_VEML6070 uv = Adafruit_VEML6070();

//RGB sensor parameters ------------------------
SFE_ISL29125 RGB_sensor;// Declare sensor object

//VOCS sensor parameters ------------------------
Adafruit_CCS811 ccs;
float temp;
//INTEGERS to be SEND ---------------------------------

int UV,VOCS,CO2; //integers to be send -  UV intensity,vocs(ppb), co2(ppm),RED, GREEN, BLUE 


//Radio Parameters -------------------------
/* for feather m0  */
#define RFM95_CS 8
#define RFM95_RST 4
#define RFM95_INT 3

// Change to 434.0 or other frequency, must match RX's freq!
#define RF95_FREQ 433.5
// Singleton instance of the radio driver
RH_RF95 rf95(RFM95_CS, RFM95_INT);

char* edafos;
char serialdata[14]; //  This is the buffer of the serial port
char apostoliC[80];

char message1[]={"Payload_Reply1"};
char message2[]={"Payload_Reply2"};
char message3[]={""};
char message4[]={"Dump_SD_serial"};
char message5[]={"Erase__SD_data"};

void setup()
{
  
  //Initialize serial connection for debugging
  Serial.begin(9600);
     
 // UV  VEML6070 SETUP ---------------
  uv.begin(VEML6070_4_T);  // pass in the integration time constant. max integration time/ per measurement (500msec)

 // RGB sensor SETUP ---------------
 if (RGB_sensor.init())
  { Serial.println("Sensor Initialization Successful\n\r");  }

 // VOCS sensor SETUP ---------------
if(!ccs.begin()){
    Serial.println("Failed to start sensor! Please check your wiring.");
   // while(1);
  }
  //calibrate temperature sensor
  while(!ccs.available());
  float temp = ccs.calculateTemperature();
  ccs.setTempOffset(temp - 25.0);


  //Radio SETUP ---------------

  pinMode(RFM95_RST, OUTPUT);
  digitalWrite(RFM95_RST, HIGH);

  //while (!Serial);
  Serial.begin(9600);
  delay(100);

  Serial.println("Feather LoRa TX Test!");

  // manual reset
  digitalWrite(RFM95_RST, LOW);
  delay(10);
  digitalWrite(RFM95_RST, HIGH);
  delay(10);

  while (!rf95.init()) {
    Serial.println("LoRa radio init failed");
    //while (1);
  }
  Serial.println("LoRa transmit radio init OK!");

  // Defaults after init are 434.0MHz, modulation GFSK_Rb250Fd250, +13dbM
  if (!rf95.setFrequency(RF95_FREQ)) {
    Serial.println("setFrequency failed");
    //while (1);
  }
  Serial.print("Set Freq to: "); Serial.println(RF95_FREQ);
  
  // Defaults after init are 434.0MHz, 13dBm, Bw = 125 kHz, Cr = 4/5, Sf = 128chips/symbol, CRC on

  // The default transmitter power is 13dBm, using PA_BOOST.
  // If you are using RFM95/96/97/98 modules which uses the PA_BOOST transmitter pin, then 
  // you can set transmitter powers from 5 to 23 dBm:
  rf95.setTxPower(23, false);

  delay(500); //for everything to initialize 

  //SD Card SETUP ---------------
 
 // put after Radio initiallization
 //8 is the actual CS pin for the feather. 
 //It is inaccesible and used by the radio but must be HIGH in order for sd to work no matter what CS pin for sd is used.
  // pinMode(8, OUTPUT);//unrem if radio off
  //digitalWrite(8, HIGH);//unrem if radio off
  Serial.print("Initializing SD card...");
  if (!SD.begin(chipSelect)) {
    Serial.println("initialization failed!");
   // return;
  }
  else {
  Serial.println("initialization done.");
  }
  
 //Timers SETUP --------------- 
 beforeMillis = 0;
  t.every(650000, payload); //every when execute the function steilepayload
  
}
//^^^^^^^^^^^^^^^^^^^^^^^^^^^^^^ VOID LOOP ^^^^^^^^^^^^^^^^^^^^^^^^^^^^^^^^^^^^^^
void loop()
{
 
 
 // --------------  sequence of synchronisation when command t is received
 afterMillis = millis();
 duration = afterMillis - beforeMillis;
 
 if ((unsigned long)duration >= 6500) 
 {
  payload();
  beforeMillis = millis();
  t.update(); //update timer if we dont use it it bugs ---> millis().
    }
  
 // -------If any command was received... ------------
    
    uint8_t buf[RH_RF95_MAX_MESSAGE_LEN];
    uint8_t len = sizeof(buf);

    if (rf95.recv(buf, &len)) 
   {
           
      Serial.print("RSSI,");
      Serial.print(rf95.lastRssi(), DEC);Serial.print(",");
      Serial.println((char*)buf);

 /*     File dataFile = SD.open("datalog.txt", FILE_WRITE);
     // Everything received from the radio module is also saved on the sd card. In this  way we backup each modules data to both modules
     if (dataFile) {
    dataFile.println((char*)buf);
    dataFile.close();
    }   */
      memcpy(trig, &buf[0], 1 );//Acquire the first character of the buffer
      trig[2] = '\0';
   
    }
         if (strlen((char*)buf) > 0)
      { 
         if (strcmp_P((char*)trig, "t") == 0)    // If the first character of rxbuffer is t then you also send 
          { 
           delay(300);
           payload();
           beforeMillis = millis();  //Reset everything to zero
           }
        else if (strcmp_P((char*)buf, "Pcomtest") == 0)
          { 
          Pcomtest();
          }
         /*
         else if (strcmp_P((char*)buf, "entoli3") == 0)
          {
          
          }  */
         else if (strcmp_P((char*)buf, "PdumpSD") == 0)
          {
          PdumpSD();
          }
         else if (strcmp_P((char*)buf, "PdeleteSD") == 0)
          {
          PdeleteSD();
          }
         }
    void clearRxBuf(); //Clear receive buffer
    memset(buf, 0, sizeof(buf)); //Delete of variable buf

      //-----------------receive command from serial ----------------------

    while(Serial.available()) {     //As long as there is data in serial port
       Serial.readBytes(serialdata, 14); //We use readbytes as it used below for beaming to the CanSat,  Serial.readString is not converted
       Serial.println(serialdata);

    if (strcmp_P((char*)serialdata, "PdumpSD") == 0) {
      PdumpSD();
    }
      if (strcmp_P((char*)serialdata, "PdeleteSD") == 0){
      PdeleteSD();
    }
    if (strcmp_P((char*)serialdata, "Pcomtest") == 0){
      Pcomtest();
    }
    }  
    memset(serialdata, 0, sizeof(serialdata)); //Deletes the variable serialdata
 }

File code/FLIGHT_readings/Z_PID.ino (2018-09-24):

//============================functions related to autonomous flight==========================================

//---------------dataGPS-----------------------------
void pidfunction()
{
  if (GPS.fix) {

    // float fLat = decimalDegrees(GPS.latitude, GPS.lat); // Converting to DecimalDegrees with the use of a function in the end
    //  float fLon = decimalDegrees(GPS.longitude, GPS.lon);

    float fLat = GPS.latitudeDegrees; // Convertion to DecimalDegrees by the Gps module
    float fLon = GPS.longitudeDegrees;

    tripDistance = (double)calc_dist(fLat, fLon, targetLat, targetLon); //calculate distance

    if ((calc_bearing(fLat, fLon, targetLat, targetLon)) > 0) {       //calculate heading with function at the end.
      fHeading = (float)calc_bearing(fLat, fLon, targetLat, targetLon);
    }
    else {                                                            // For western hemisphere
      fHeading = (int)calc_bearing(fLat, fLon, targetLat, targetLon) + 360;
    }

    //  Serial.println(double(calc_bearing(fLat, fLon, targetLat, targetLon)));
    heading = int(fHeading);
    dist = long(tripDistance);
  }
  //descent rate calculation
  int drop = Apold - Ap; //calculate drop in 1 sec
  int droptime = Ap / drop; //calculate projected drop time
  float d = GPS.speed * 0.51444444444444;  //το GPS.speed is in  knots converted to m/second
  int Speed = int(d);
  int travel = Speed * droptime; //projected distance at this speed.

  //****Data received from BNO*****************
  sensors_event_t event;
  bno.getEvent(&event);
  uint8_t system, gyro, accel, mag;
  system = gyro = accel = mag = 0;
  bno.getCalibration(&system, &gyro, &accel, &mag);

  //Serial.println(system, DEC);//calibration value
  int calib = (system, DEC);
  //Serial.println(event.orientation.x, 4);//heading in Χ Axis

  //******Choise of absolute heading******

  float realheading; // real heading 
  if (calib < 1) // If the Bno sensor  is not yet fully calibrated (0 being bad and 3 perfect)
  {
    realheading = GPS.angle; // The value received is the angle  in relation to north received from the gps
  }
  else {
    realheading = event.orientation.x;// If bno is calibrated use the value from Bno sensor
  }

  //*****Sets the desired heading value for the target. (calculated by gps)************ 

  float headingDiff = fHeading - realheading;//headingdiff(Difference between desired and real heading) Difference between desired and real heading

  //If value is negative we must turn left  -------- If value is positive we must turn right


  if (headingDiff > 180) //If difference bigger than 180 degrees
    headingDiff = -360 + headingDiff; //We substract 360 to receive the smallest absolute number (+ or -) 
  if (headingDiff < -180) //εάν η διαφορά είναι μικρότερη από -180
    headingDiff = 360 + headingDiff; // We add 360 to receive the smallest absolute number (+ or -)
  // If nothing of the above is used the value remains unchanged
  //(Positive left, Negative right)

  //  headingDiff = 19 ;//testing
  // PIDstatus = 21; //testing

  /*  if (-181 < testDiff && testDiff < 179)      //testing
    {
      testDiff = testDiff + 5; //testing
    }
    else
    { testDiff = -180 ;
    }  */



  // headingDiff = testDiff; //testing
  int intDiff = (int)headingDiff; // convert float to int for calculations


  // Serial.println(PIDstatus);
  // Serial.println(maxAngle);

  if (PIDstatus == 31)
  {
    //max range protection 
    if (travel > 700)
    {
      myservoL.write(5); //left servo not pulling
      myservoR.write(55);
      }
    else{  
    if (20 < headingDiff && headingDiff < 180) //Have turn right
    {
      myservoL.write(5); //left servo not pulling
      myservoR.write(115 - maxAngle);
    }
    if (0 < headingDiff && headingDiff < 19) //bellow 20 degrees
    {
      myservoL.write(5); //Nothing
      myservoR.write(115);
    }

    if (-20 > headingDiff && headingDiff > -180) // Have to turn left
    {
      myservoL.write(5 + maxAngle);
      myservoR.write(115);//Right servo not pulling
    }
    if (0 > headingDiff && headingDiff > -19) //Bellow 20 degrees
    {
      myservoL.write(5);
      myservoR.write(115);//Noting
    }
  }
  }
  else if (PIDstatus == 24)
  {
    //on off autoturning with +-20 no action angle
    if (20 < headingDiff && headingDiff < 180) //Want to turn right
    {
      myservoL.write(5); //Left servo not pulling
      myservoR.write(115 - maxAngle);
    }
    if (0 < headingDiff && headingDiff < 19) //Bellow 20 degrees
    {
      myservoL.write(5); //Nothing
      myservoR.write(115);
    }

    if (-20 > headingDiff && headingDiff > -180) //Want to turn right
    {
      myservoL.write(5 + maxAngle);
      myservoR.write(115);//Left serbo not pulling
    }
    if (0 > headingDiff && headingDiff > -19) //Bellon 20 degrees
    {
      myservoL.write(5);
      myservoR.write(115);//Nothing
    }
  }
  else if (PIDstatus == 23)
  {
    //analog autoturning with bigger initial starting angle
    int turn; //How much it will turn
    turn = (maxAngle - 50) * abs(intDiff) / 180; //Same as max angle multiplied by diversion( without a negative or positive sign) devided by 180. 
    //Serial.println(turn);

    if (20 < headingDiff && headingDiff < 180) //Want to turn right
    {
      myservoL.write(5); //Left servo is not pulling
      myservoR.write(65 - turn);
    }
    if (0 < headingDiff && headingDiff < 19) //Want to turn right
    {
      myservoL.write(5); //Left servo not pulling
      myservoR.write(95);
    }

    if (-20 > headingDiff && headingDiff > -180) //Want to turn right
    {
      myservoL.write(55 + turn);
      myservoR.write(115);//Right servo not pulling
    }
    if (0 > headingDiff && headingDiff > -19) //Want to turn right
    {
      myservoL.write(25);
      myservoR.write(115);//Right servo not pulling
    }
  }
  else if (PIDstatus == 22)
  {
    //Analog autoturning
    int turn; //πόσο θα στρίψει
    turn = maxAngle * abs(intDiff) / 180;  //Same as max angle multiplied by diversion( without a negative or positive sign) devided by 180.
    Serial.println(turn);

    if (0 < headingDiff && headingDiff < 180) //Want to turn right
    {
      myservoL.write(5); //Left servo not pulling
      myservoR.write(115 - turn);
    }

    if (0 > headingDiff && headingDiff > -180) //Want to turn right
    {
      myservoL.write(5 + turn);
      myservoR.write(115);//Right servo not pulling
    }
  }
  else if (PIDstatus == 21)
  {
    //autoturning no PID
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
